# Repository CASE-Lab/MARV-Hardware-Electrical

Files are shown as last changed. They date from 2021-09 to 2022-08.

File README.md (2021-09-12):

# MARV-Hardware-Electrical
Contains the electrical design files fo the MARV system. These includes the PCBs and system wiring diagram and specific wire function diagram. Some of the PCB projects includes a component library, otherwise the CASE-Association case-eagle-libraries have been used, found here: https://github.com/CASE-Association/case-eagle-libraries.git

This project uses both Eagle and KiCad ECAD programs. This is shown by folder names.

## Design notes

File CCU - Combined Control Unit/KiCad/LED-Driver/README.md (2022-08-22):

# MIDI Fuse LED Driver

Led driver with integrated eFuse and PWM dimming in a MIDI fuse format. Provides undervoltage cutoff for battery protection and a low standby current of 30 uA.

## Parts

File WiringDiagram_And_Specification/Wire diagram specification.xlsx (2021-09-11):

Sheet: Wire diagram specification
Reference | Name | Number of wires | Function | Connector 1 | Pin on Connector 1 | Wire color | Wire Marking | Connector 2 | Pin on Connector 2 | Flag | Length | AWG/mm^2 | DR Shrink | Est Length (m) | Total Est Length (m) | Bundle Diameter (mm) | Bundle Diameter | Deutsch Contact Type1 | Deutsch Contact Type2
Drive-By-Wire system
W1 | APS ECM (OUT) | 9 | APS 1 - VCC 5V | DTM04-12PA | 1 | White | VCC1 | DRC26-50S01 | 34 | W1, APS ECM | 0.9 m | 18 AWG | Type 3/8 (0.375) | 0.7 | 6.3 | 5.4 | 0.212598425 | 0462-005-20141 (DTM/DRC,F) | 0462-005-20141 (DTM/DRC,F)
 |  |  | APS 1 - GND |  | 2 | White | GND1 |  | 24
 |  |  | APS 1 - Signal |  | 3 | White | SIG1 |  | 14
 |  |  | APS 2 - VCC 5V |  | 4 | White | VCC2 |  | 23
 |  |  | APS 2 - GND |  | 6 | White | GND2 |  | 13
 |  |  | APS 2 - Signal |  | 5 | White | SIG2 |  | 4
 |  |  | APS Fully closed/open - VCC 5V |  | 7 | White | VCC3 |  | 12
 |  |  | APS Fully closed/open - GND |  | 8 | White | GND3 |  | 2
 |  |  | APS Fully closed/open - Signal |  | 9 | White | SIG3 |  | 3
W2 | APS Handle (IN) | 9 | APS 1 - VCC 5V | DTM06-12SA | 1 | White | VCC1 | DRC26-50S01 | 43 | W2, APS HAND | 0.9 m | 18 AWG | Type 3/8 (0.375) | 0.7 | 6.3 |  |  | 0460-010-20141 (DTM/DRC,M) | 0462-005-20141 (DTM/DRC,F)
 |  |  | APS 1 - GND |  | 2 | White | GND1 |  | 33
 |  |  | APS 1 - Signal |  | 3 | White | SIG1 |  | 42
 |  |  | APS 2 - VCC 5V |  | 4 | White | VCC2 |  | 32
 |  |  | APS 2 - GND |  | 6 | White | GND2 |  | 22
 |  |  | APS 2 - Signal |  | 5 | White | SIG2 |  | 41
 |  |  | APS Fully closed/open - VCC 5V |  | 7 | White | VCC3 |  | 21
 |  |  | APS Fully closed/open - GND |  | 8 | White | GND3 |  | 11
 |  |  | APS Fully closed/open - Signal |  | 9 | White | SIG3 |  | 31
W3 | RPS ECM (OUT) | 6 | RPS 1 - VCC 5V | DTM04-08PA | 1 | White | VCC1 | DRC26-50S01 | 48 | W3, RPS ECM | 0.9 m | 18 AWG | Type 1/4 (0.25) | 0.7 | 4.2 | 4.409081537 | 0.1735858871 | 0462-005-20141 (DTM/DRC,F) | 0462-005-20141 (DTM/DRC,F)
 |  |  | RPS 1 - GND |  | 2 | White | GND1 |  | 49
 |  |  | RPS 1 - Signal |  | 3 | White | SIG1 |  | 50
 |  |  | RPS 2 - VCC 5V |  | 4 | White | VCC2 |  | 39
 |  |  | RPS 2 - GND |  | 5 | White | GND2 |  | 30
 |  |  | RPS 2 - Signal |  | 6 | White | SIG2 |  | 40
W4 | RPS Handle (IN) | 6 | RPS 1 - VCC 5V | DTM06-08SA | 1 | White | VCC1 | DRC26-50S01 | 47 | W4, RPS HAND | 0.9 m | 18 AWG | Type 1/4 (0.25) | 0.7 | 4.2 |  |  | 0460-010-20141 (DTM/DRC,M) | 0462-005-20141 (DTM/DRC,F)
 |  |  | RPS 1 - GND |  | 2 | White | GND1 |  | 38
 |  |  | RPS 1 - Signal |  | 3 | White | SIG1 |  | 37
 |  |  | RPS 2 - VCC 5V |  | 4 | White | VCC2 |  | 28
 |  |  | RPS 2 - GND |  | 5 | White | GND2 |  | 29
 |  |  | RPS 2 - Signal |  | 6 | White | SIG2 |  | 27
W5 | BUZZER ECM | 2 | VCC 12V | DTM04-3P | 1 | White | VCC | DRC26-50S01 | 16 | W5, BUZ ECM | 0.9 m | 18 AWG | Type 1/8 (0.125) | 0.7 | 1.4 | 2.545584412 | 0.1002198586 | 0462-005-20141 (DTM/DRC,F) | 0462-005-20141 (DTM/DRC,F)
 |  |  | GND |  | 2 | White | GND |  | 17
W6 | BUZZER Handle | 2 | VCC 12V | DTM06-3S | 1 | White | VCC | DRC26-50S01 | 6 | W6, BUZ HAND | 0.9 m | 18 AWG | Type 1/8 (0.125) | 0.7 | 1.4 |  |  | 0460-010-20141 (DTM/DRC,M) | 0462-005-20141 (DTM/DRC,F)
 |  |  | GND |  | 2 | White | GND |  | 7
W7 | Paddel Wheel ECM | 3 | VCC - 12V | DTM04-3P | 1 | White | VCC | DRC26-50S01 | 18 | W7, PW ECM | 0.9 m | 18 AWG | Type 3/16 (0.1875) | 0.7 | 2.1 | 3.117691454 | 0.1227437579 | 0462-005-20141 (DTM/DRC,F) | 0462-005-20141 (DTM/DRC,F)
 |  |  | GND |  | 2 | White | GND |  | 19
 |  |  | Signal |  | 3 | White | SIG |  | 20
W8 | Paddel Wheel Sensor | 3 | VCC - 12V | DTM06-3S | 1 | White | VCC | DRC26-50S01 | 8 | W8, PW SENS | 0.9 m | 18 AWG | Type 3/16 (0.1875) | 0.7 | 2.1 |  |  | 0460-010-20141 (DTM/DRC,M) | 0462-005-20141 (DTM/DRC,F)
 |  |  | GND |  | 2 | White | GND |  | 9
 |  |  | Signal |  | 3 | White | SIG |  | 10
W9 | Angle Sensor | 3 | GND | 282087-1 | 1 | White | GND | DT06-12SA | 3 | W9, ANG SENS | 0.95 m | 18 AWG | Type 3/16 (0.1875) | 1 | 3 |  |  |  | 0462-201-16141 (DT,F)
 |  |  | VCC -12V |  | 2 | White | VCC |  | 2
 |  |  | Signal |  | 3 | White | OUTPUT |  | 1
W10 | Motor | 4 | A1 | NA |  | Black | 2 | DT06-12SA | 10 | MOTOR |  |  |  | 1 | 4 |  |  |  | 0462-201-16141 (DT,F)
 |  |  | A2 |  |  | Black | 3 |  | 9
 |  |  | B1 |  |  | Black | 1 |  | 12
 |  |  | B2 |  |  | Black (Y/G) |  |  | 11
 |  |  | Cable Shield |  |  | White |  |  | 8
DB-W11 | DB Wire Harness | 6 | CAN_H | DT06-6S | 1 | Black, Yellow | CAN-H | DTM06-12SA | 1 | W11, DB | 1.2 m | 18 AWG | Type 3/8 (0.375) | 0.6 | 2.4 | 7.517978452 | 0.2959834033 | 0462-201-16141 (DT,F) | 0462-005-20141 (DTM/DRC,F)
 |  |  | CAN_L |  | 2 | Black, Green | CAN-L |  | 2 |  |  | CAN Cable |  | 0.6 | 0.6
 |  |  | 12V_AUTO |  | 3 | White | 12V-A |  | 3
 |  |  | GND |  | 4 | White | GND |  | 4
 |  |  | 12V |  | 5 | White | 12V |  | 5
 |  |  | GND |  | 6 | White | GND |  | 6
DB-W12 | DB Wire Harness | 6 | CAN_H | DTM06-12SA | 12 | Black, Yellow | CAN-H | DT06-06S-E008 | 1 | W12, DB | 2.2 m | 18 AWG | Type 3/8 (0.375) | 1.6 | 6.4 |  |  | 0462-005-20141 (DTM/DRC,F) | 0462-201-16141 (DT,F)
 |  |  | CAN_L |  | 11 | Black, Green | CAN-L |  | 2 |  |  | CAN Cable |  | 1.6 | 1.6
 |  |  | 12V_AUTO |  | 10 | White | 12V-A |  | 3
 |  |  | GND |  | 9 | White | GND |  | 4
 |  |  | 12V |  | 8 | White | 12V |  | 5
 |  |  | GND |  | 7 | White | GND |  | 6
W13 | OCU Mode Select | 4 | ? | DT06-4S | 1 | White | 1 | DT06-4S-E008 | 1 | W13, OCU MODE |  | 18 AWG | Type 1/4 (0.25) | 1 | 4 | 3.6 | 0.1417322833 | 0462-201-16141 (DT,F) | 0462-201-16141 (DT,F)
 |  |  | ? |  | 2 | White | 2 |  | 2
 |  |  | ? |  | 3 | White | 3 |  | 3
 |  |  | ? |  | 4 | White | 4 |  | 4
W14 | OCU Pedal | 2 | IN | DT06-2S-E008 | 1 | White | - | NA |  | W14, OCU PEDAL |  | 18 AWG | Type 1/8 (0.125) | 1.5 | 3 | 2.545584412 | 0.1002198586 |  | 0462-201-16141 (DT,F)
 |  |  | OUT |  | 2 | Green | -
W16 | ACU CAN | 2 | CAN_H | Y-Boot |  | Black, Yellow |  | PXMBNI12FIM04DSCPG7 | 4 | W16, ACU CAN |  | CAN Cable |  | 0.5 | 0.5 | 5.5 | 0.2165354329
 |  |  | CAN_L |  |  | Black, Green |  |  | 5
W17 | ACU Power | 4 | GND | Y-Boot |  | White | Black | T4111001041-000 | 1 | W17, ACU POW |  | 18 AWG | Type 1/4 (0.25) | 0.5 | 2 | 3.6 | 0.1417322833
 |  |  | GND |  |  | White | Black |  | 2
 |  |  | 12V |  |  | White | Red |  | 3
 |  |  | 12V |  |  | White | Red |  | 4
W18 | INS | 4 | ~~SYNC IN A – ODO B~~ | UP01L07 M010S BK1 Z2ZA | ~~1~~ | Black, Green |  | PXMBNI12FIM05ASCPG7 |  | W18, INS |  |  |  | 0.4 | 1.6 | -
 |  |  | ~~SYNC IN B – PORT B RX - ODO A ~~ |  | ~~2~~ | Black, Blue
 |  |  | VIN |  | 3 | Black, Red |  |  | 3
 |  |  | GND |  | 4 | Black, Black |  |  | 4
 |  |  | ~~PORT A RS-232/RS-422~~ |  | ~~5~~ | Black, N/A
 |  |  | ~~SYNC OUT A~~ |  | ~~6~~ | Black, Brown
 |  |  | ~~PORT E TX – PORT A RS422 TX+ ~~ |  | ~~7~~ | Black, White
 |  |  | PORT A RS232 TX – PORT A RS422 TX- |  | 8 | Black, Yellow |  |  | 1
 |  |  | PORT A RS232 RX – PORT A RS422 RX+ |  | 9 | Black, Orange |  |  | 2
 |  |  | ~~PORT E RX – PORT A RS422 RX- ~~ |  | ~~10~~ | Black, Grey
W19 | Fuse-Box-2 -> CCU | 4 | GND | DTP06-4S-E004 | 1 | Black |  | DTP06-4S-E004 | 3 | W19, PDU POW |  | 6mm2 |  | 0.5 | 2 | 8.88 | 0.3496062989 | 0462-203-12141 (DTP,F) | 0462-203-12141 (DTP,F)
 |  |  | GND |  | 2 | Black |  |  | 4
 |  |  | 12V |  | 3 | Red |  |  | 1
 |  |  | 12V |  | 4 | Red |  |  | 2
W20 | Aux battery -> Fuse-Box-2 | 2 | GND | NA | (-) | Black |  | PG7 2x | (-) | W20, AUX Bat-FB2 |  | 6mm2 |  | 0.2 | 0.4 | 6.279108217 | 0.2472089847
 |  |  | 12V |  | (+) | Red |  |  | (+)
W21 | Charger Con2 -> Aux battery | 2 | GND | DTP06-2S | 1 (-) | Black |  | NA | (-) | W21, CHA CON2-AUX Bat |  | 6mm2 |  | 3 | 6 |  |  | 0462-203-12141 (DTP,F)
 |  |  | 12V |  | 2 (+) | Red |  |  | (+)
W22 | Charger -> Charger Con2 | 2 | GND | NA | (-) | Black |  | DTP04-2P | 1 (-) | W22, CHA-CHA CON2 |  | 6mm2 |  | 0.2 | 0.4 |  |  |  | 0460-204-12141 (DTP,M)
 |  |  | 12V |  | (+) | Red |  |  | 2 (+)
W23 | Charger Con1 -> Charger | 2 | GND | DTP04-2P | 1 (-) | Black |  | NA | (-) | W23, CHA CON1-CHA |  | 6mm2 |  | 0.2 | 0.4 |  |  | 0460-204-12141 (DTP,M)
 |  |  | 12V |  | 2 (+) | Red |  |  | (+)
W24 | Fuse-Box-1 -> Charger Con1 | 2 | GND | DTP06-4S | 1 (-) | Black |  | DTP06-2S | 1 (-) | W24, FB1-CHA CON1 |  | 6mm2 |  | 0.4 | 0.8 |  |  | 0462-203-12141 (DTP,F) | 0462-203-12141 (DTP,F)
 |  |  | 12V |  | 3 (+) | Red |  |  | 2 (+)
W25 | Fuse-Box-1 -> Charge Battery Connector | 2 | GND | Ring Terminal M5 | B_OUT | White |  | DTP06-2S | 1 (-) | W25, CHARGER IN |  | 4mm2 |  | 1.5 | 3 |  |  | 0462-203-12141 (DTP,F) | 0462-203-12141 (DTP,F)
 |  |  | 12V | Ring Terminal M5 | A_OUT | White |  |  | 2 (+)
W26 | Start Battery -> Fuse-Box-1 | 2 | GND | NA | (-) | Black |  | PG7 2x | (-) | W26, STA BAT |  | 6mm2 |  | 0.5 | 1
 |  |  | 12V |  | (+) | Red |  |  | (+)
W27 | Fuse-Box-2 -> LED Button/Connectors | 4 | GND | NA | (-) | Black |  | DTM04-2PA 2x | 1 | W27, LED FB |  | 6mm2 |  | 0.5 | 2
 |  |  | GND |  | (-) | Black |  |  | 1
 |  |  | 12V |  | (+) | Red |  |  | 2
 |  |  | 12V |  | (+) | Red |  |  | 2
W28 | LED Back | 2 | GND | DTM04-2PA | 1 | Black |  | DTM06-2SA | 1 | W28, LED BCK |  | 6mm2 |  | 0.5 | 1
 |  |  | 12V |  | 2 | Red |  |  | 2
W29 | LED Front | 2 | GND | DTM04-2PA | 1 | Black |  | DTM06-2SA | 1 | W29, LED FRT |  | 6mm2 |  | 0.5 | 1
 |  |  | 12V |  | 2 | Red |  |  | 2
WaveRunner to Drive-By-Wire system
W27,W28 | APS | 9 | APS 1 - VCC 5V | DTM04-12PA, DTM06-12SA | 1 | (O/R) - Orange/Red |  |  |  | W27, APS ECM / W28, APS HAND
 |  |  | APS 1 - GND |  | 2 | (B/R) - Black/Red
 |  |  | APS 1 - Signal |  | 3 | (P/R) - Pink/Red
 |  |  | APS 2 - VCC 5V |  | 4 | (O/W) - Orange/White
 |  |  | APS 2 - Signal |  | 6 | (P/W) - Pink/White
 |  |  | APS 2 - GND |  | 5 | (B/W) - Black/White
 |  |  | APS Fully closed/open - VCC 5V |  | 7 | (O/G) - Orange/Green
 |  |  | APS Fully closed/open - GND |  | 8 | (B/G) - Black/Green
 |  |  | APS Fully closed/open - Signal |  | 9 | (P/G) - Pink/Green
W29/W30 | RPS | 6 | RPS 1 - VCC 5V | DTM04-08PA, DTM06-08SA | 1 | (O/R) - Orange/Red |  |  |  | W29, RPS ECM / W30, RPS HAND
 |  |  | RPS 1 - GND |  | 2 | (B/R) - Black/Red
 |  |  | RPS 1 - Signal |  | 3 | (P/R) - Pink/Red
 |  |  | RPS 2 - VCC 5V |  | 4 | (O/W) - Orange/White
 |  |  | RPS 2 - GND |  | 5 | (B/W) - Black/White
 |  |  | RPS 2 - Signal |  | 6 | (P/W) - Pink/White
W31/W32 | Buzzer | 2 | VCC - 12V | DTM04-3P, DTM06-3S | 1 | (R) - Red |  |  |  | W31, BUZ ECM / W32, BUZ HAND
 |  |  | GND |  | 2 | (B) - Black
W33/W34 | Paddel Wheel | 3 | VCC - 12V | DTM04-3P, DTM06-3S | 1 | (R/W) - Red/White (or Red/Yellow) |  |  |  | W33, PW ECM / W34, PW SENS
 |  |  | GND |  | 2 | (B/Y) - Black/Yellow
 |  |  | Signal |  | 3 | (Y) - Yellow
WaveRunner - Decawave Positioning System
W35 | ACU USB -> Decawave Hub Unit (DHU) | 5 | VCC - 5V | ACU USB1 - (Cable PX0441/2M00) | 1 | Red |  | PX0446 | 1 | W35, DHU
 |  |  | D- |  | 2 | White |  |  | 2
 |  |  | D+ |  | 3 | Green |  |  | 3
 |  |  | GND |  | 4 | Black |  |  | 4
 |  |  | Shield |  | 5 | Black |  |  | 5
W36/W37/W38 | DHU -> Decawave Sensor Unit (DSU), Anchors | 8 | GND | Cable Gland - (Cable 1404181) | 1 | White |  | PXMBNI08FPF08AFLM11002 | 1 | W36, DSU_A1 / W37, DSU_A2, W38, DSU_A3
 |  |  | VCC - 5V |  | 2 | Brown |  |  | 2
 |  |  | RS_232_TX (DHU) |  | 3 | Green |  |  | 3
 |  |  | RS_232_RX (DHU) |  | 4 | Yellow |  |  | 4
 |  |  | SWDIO |  |  | Grey |  |  | 5
 |  |  | SWCLK |  |  | Pink |  |  | 6
 |  |  | NRST |  |  | Blue |  |  | 7
W39 | ACU ES -> Decawave Sensor Unit, Passive tag | 8 | GND | PXMBNI12FIM05BSCPG7 | 4 | White |  | PXMBNI08FPF08AFLM11002 | 1 | W39, DSU_PT
 |  |  | VCC - 5V |  | 3 | Brown |  |  | 2
 |  |  | RS_232_TX (ACU ES) |  | 2 | Green |  |  | 3
 |  |  | RS_232_RX (ACU ES) |  | 1 | Yellow |  |  | 4
 |  |  | SWDIO |  |  | Grey |  |  | 5
 |  |  | SWCLK |  |  | Pink |  |  | 6
 |  |  | NRST |  |  | Blue |  |  | 7
 |  |  |  |  |  | Red |  |  | 8
W40/W41 | DHU Harbour -> DSU Harbour tags | 8 | GND | Cable Gland - (Cable 1404181) | 1 | White |  | PXMBNI08FPF08AFLM11002 | 1 | W40, DSU_T1 / W41, DSU_T2
 |  |  | VCC - 5V |  | 2 | Brown |  |  | 2
 |  |  | RS_232_TX (DHU) |  | 3 | Green |  |  | 3
 |  |  | RS_232_RX (DHU) |  | 4 | Yellow |  |  | 4
 |  |  | SWDIO |  |  | Grey |  |  | 5
 |  |  | SWCLK |  |  | Pink |  |  | 6
 |  |  | NRST |  |  | Blue |  |  | 7
 |  |  |  |  |  | Red |  |  | 8

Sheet: Pins, Tube, Wire length
Cable Types | Cable Diameter (mm) | Total Cable Length | DR25 Types | Total DR25 Length | Contact Types | Deutsch Nbr of Contacts | Deutsch Sealing Plugs
CAN Cable | 5.5 | 2.7 | Type 1/8 (0.125) | 2.9 | 0462-005-20141 (DTM/DRC,F) | 72 | 0413-204-2005 (DTM/DRC) = 35
18 AWG | 1.5 | 48.8 | Type 3/16 (0.1875) | 2.4 | 0460-010-20141 (DTM/DRC,M) | 20 | 0413-003-1605 (DT) = 25
6mm2 | 3.7 | 15 | Type 1/4 (0.25) | 2.9 | 0462-201-16141 (DT,F) | 29 | 114017-ZZ (DTP) = 6
 |  |  | Type 3/8 (0.375) | 3.6 | 0460-202-16141 (DT,M) | 0
 |  |  | Type 1/2 (0.5) | 0 | 0462-203-12141 (DTP,F) | 18
 |  |  |  |  | 0460-204-12141 (DTP,M) | 4

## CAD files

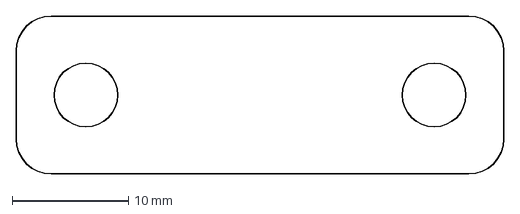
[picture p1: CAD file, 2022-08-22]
CCU - Combined Control Unit/KiCad/LED-Driver/fuseMIDIOutline.dxf
42.0 x 13.6 mm

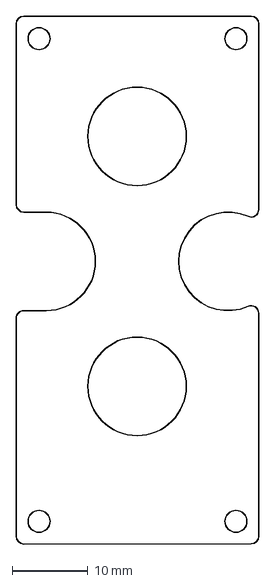
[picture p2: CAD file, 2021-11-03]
OCU - Operator Control Unit/Eagle/OCU_Buttons_Adapter_Rev1/BUTTONS_ADAPTER_PCB_OULINE.dxf
32.0 x 69.7 mm

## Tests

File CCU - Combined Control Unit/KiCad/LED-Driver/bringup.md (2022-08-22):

# Bringup notes LED Driver

## REV 1

* 68 nF for 180 Hz PWM frequency (with 100 k potentiometer)
* Approx 30 uA off current when switch open (off)
* Approx 400 uA (higher than expected?) when switch closed and battery in undervoltage (set to 10 V).
* Solid on/off operation at 13.2 volt and above. There is a band where PWM operation seems unreliable but still not clear why (Dampening decoupling needed?)?

- [ ] Check what the calculated on/off voltages should be
- [ ] Try with long LED strip to verify stability

If the PWM circuit gives to much trouble just convert to on/off control only by removing and installing jumper instead of mosfet.

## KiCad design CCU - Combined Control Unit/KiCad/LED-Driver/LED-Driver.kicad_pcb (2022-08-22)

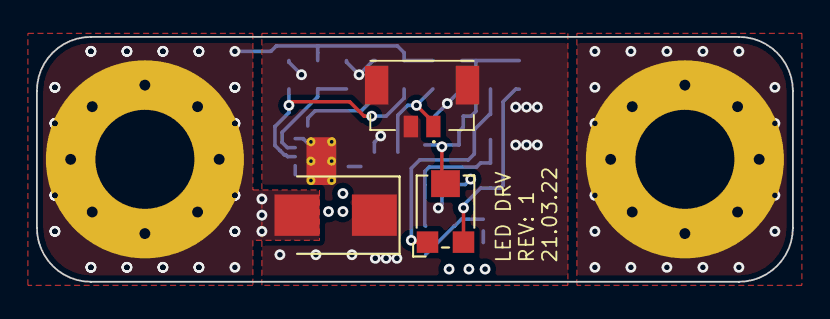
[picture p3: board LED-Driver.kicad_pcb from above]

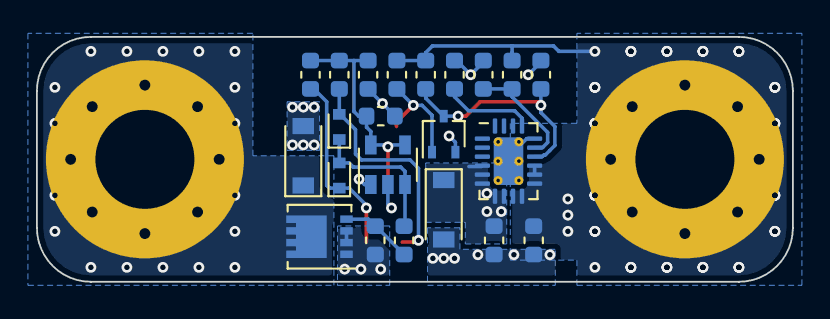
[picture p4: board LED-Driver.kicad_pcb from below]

Board: 4 copper layers, 42.0 x 13.6 mm, 27 parts (22 on the bottom side), 13 nets.

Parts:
C1, C2: 0.1 uF; C_0603_1608Metric
C3: 2.2uF 16V; C_0603_1608Metric
C4: ?; C_0603_1608Metric
D1, D5: D_Schottky; D_SOD-123
D2, D3: RB751S40T5G; D_SOD-523
D4: D_TVS; D_SMB
J1, J2: Conn_01x01; MountingHole_5.5mm_Pad_Via
J3: Conn_01x02; Molex_Micro-Lock_5055680271_1x02_P1.25_Vertical
Q1: 2N7002PW; SOT-323_SC-70
Q2: DMP3013SFV; Diodes_PowerDI3333-8
R1: 130k; R_0603_1608Metric
R2, R5: 1.5M; R_0603_1608Metric
R3, R6, R9: 100k; R_0603_1608Metric
R4: 18k; R_0603_1608Metric
R7, R8: R; R_0603_1608Metric
R10: 1k; R_0603_1608Metric
RV1: 100k; Potentiometer_Bourns_TC33X_Vertical
U1: MIC1555YM5-TR; SOT-23-5
U2: TPS25940x-Q1; QFN-20-1EP_3x4mm_P0.5mm_EP1.65x2.65mm_ThermalVias

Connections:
+12V: C1.1, D1.1, Q2.1, Q2.2, Q2.3, R9.2, U1.1, U2.4, U2.5, U2.6, U2.7, U2.8
+BATT: C2.1, D4.2, J1.1, R2.1, R5.1, R6.1, U2.9, U2.10, U2.11, U2.12, U2.13
/GATE: Q2.4, R9.1, R10.1
/LED_OUT: D5.1, J2.1, Q2.5
/PWM: D2.2, D3.1, R10.2, U1.3
/TRG_THR: C3.1, C4.1, R7.2, R8.2, RV1.2, U1.4, U1.5
/eFuse/~EN: J3.1, Q1.1, R6.2
GND: C1.2, C2.2, C3.2, C4.2, D1.2, D4.1, D5.2, J3.2, J3.MP, Q1.2, R1.2, R3.2, R4.2, U1.2, U2.16, U2.21
unnamed: D2.1, R7.1, RV1.3
unnamed: D3.2, R8.1, RV1.1
unnamed: Q1.3, R1.1, R5.2, U2.14
unnamed: R2.2, R3.1, U2.15
unnamed: R4.1, U2.17

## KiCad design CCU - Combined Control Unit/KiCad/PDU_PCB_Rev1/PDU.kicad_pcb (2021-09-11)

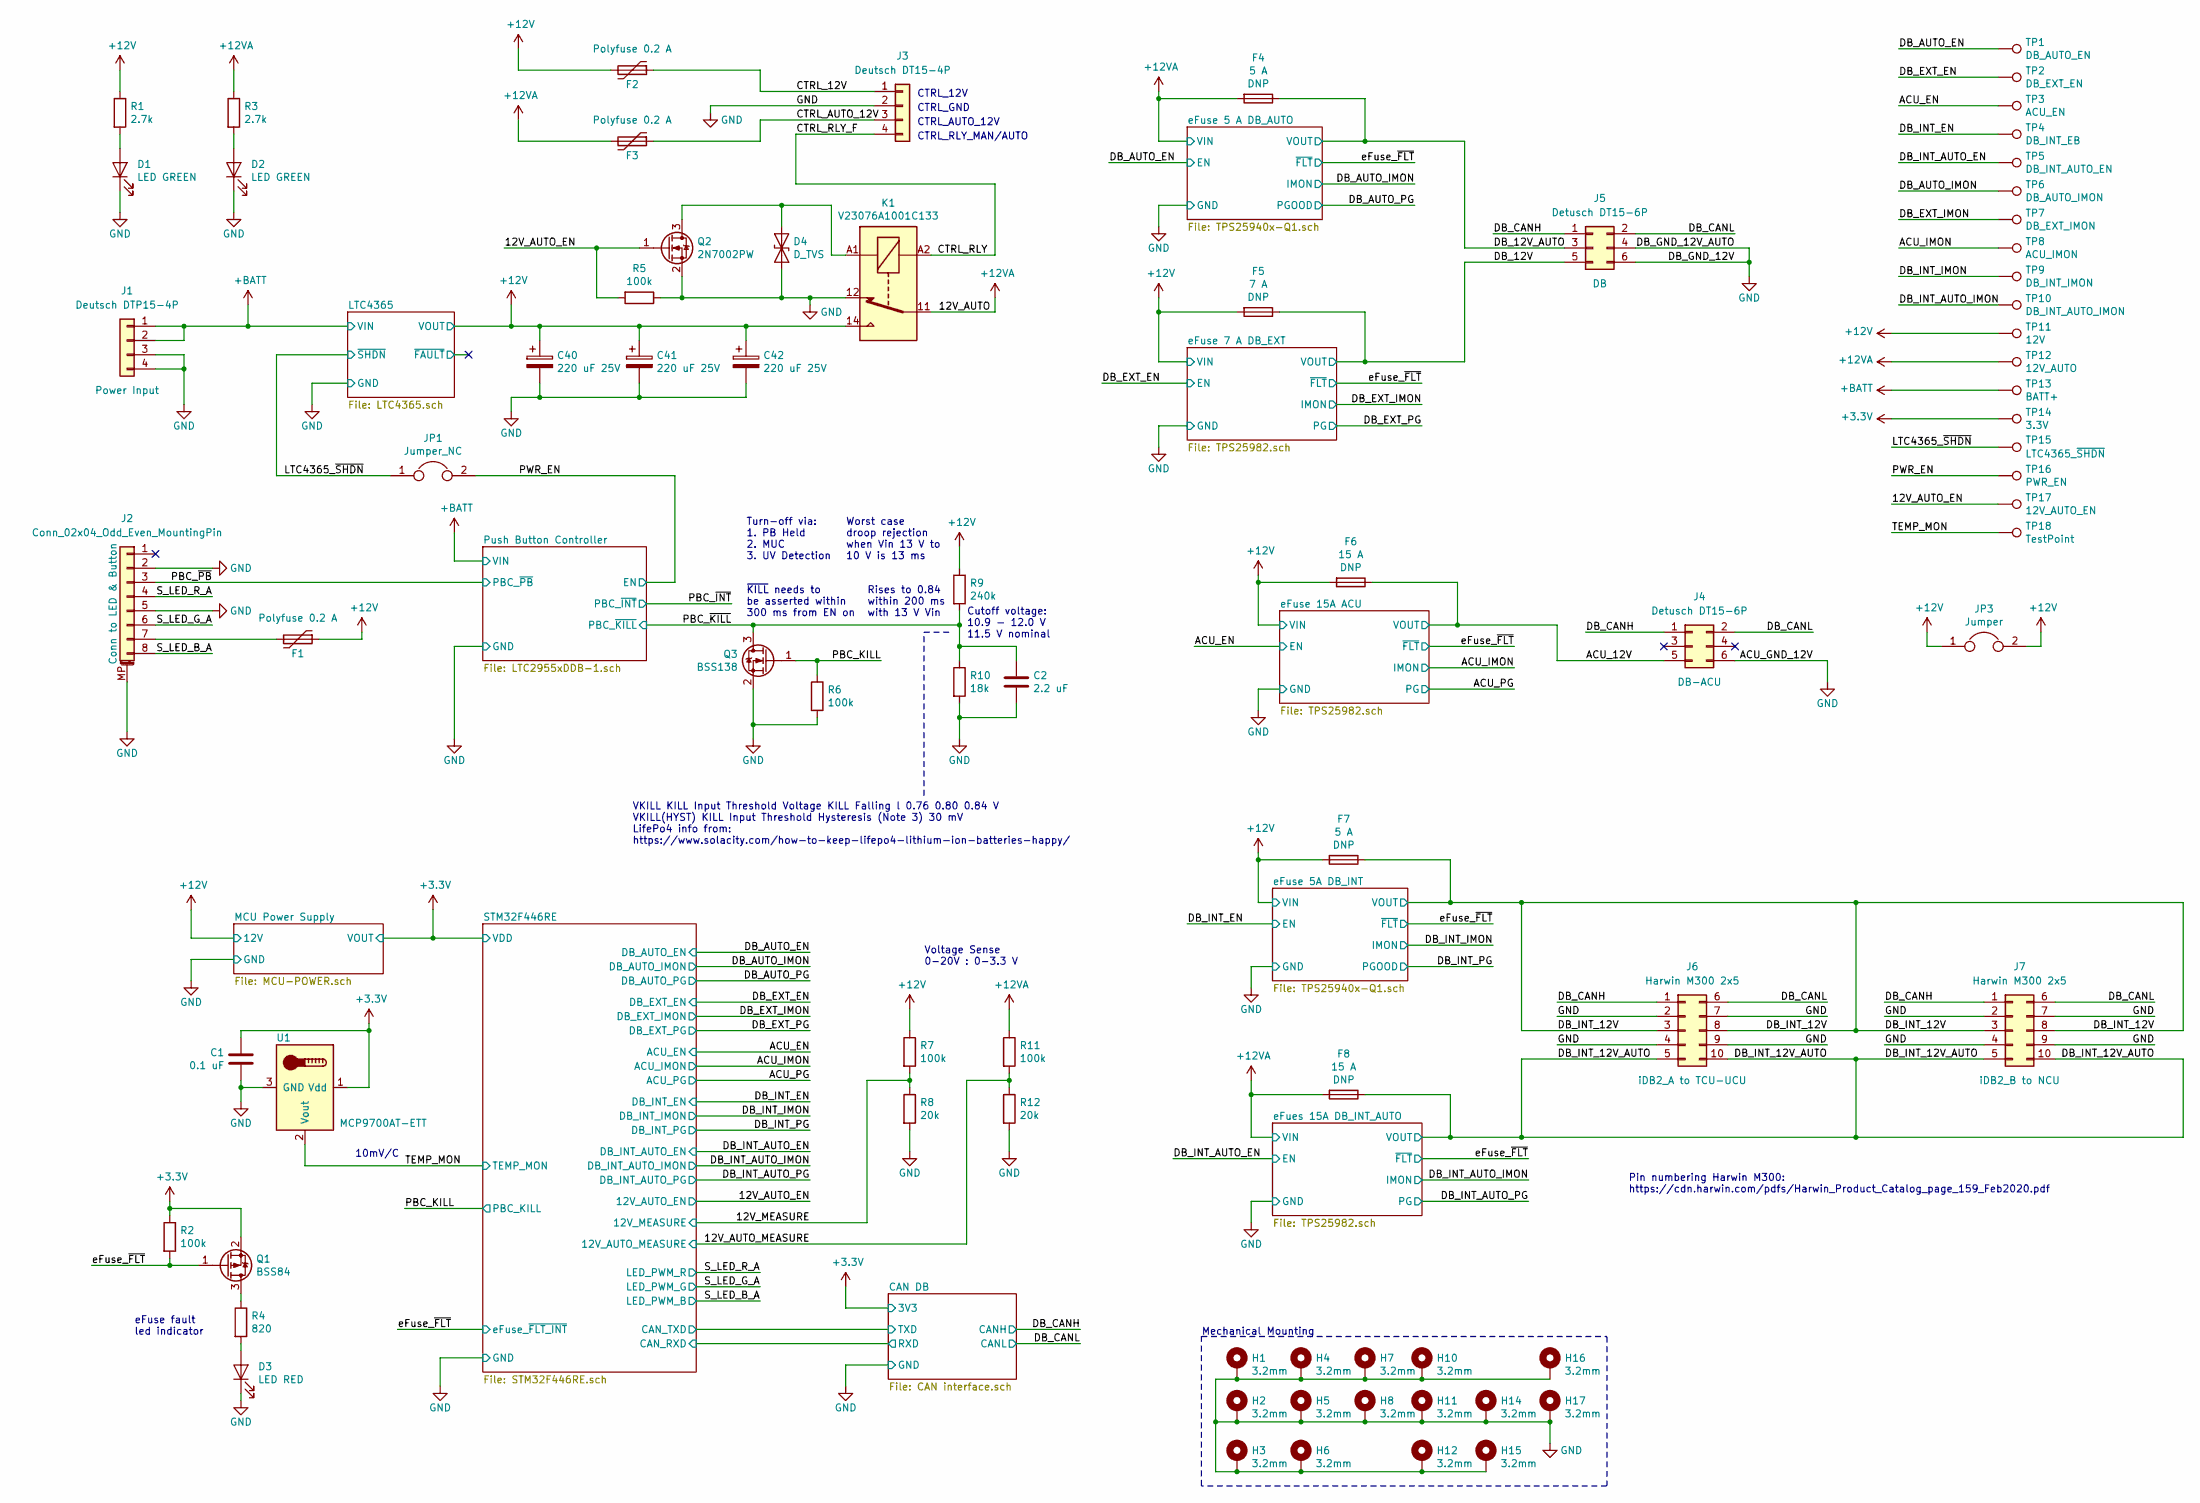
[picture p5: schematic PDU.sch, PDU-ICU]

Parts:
C1: 0.1 uF; C_0603_1608Metric
C2: 2.2 uF; C_0603_1608Metric
C40, C41, C42: 220 uF 25V; CP_Radial_D8.0mm_P3.50mm; MPN ESE227M025AG3AA
D1, D2: LED GREEN; LED_0603_1608Metric
D3: LED RED; LED_0603_1608Metric
D4: D_TVS; D_SMB; MPN TPSMB20CA
F1, F2, F3: Polyfuse 0.2 A; R_1206_3216Metric; MPN NANOSMDC020F-2
F4, F7: 5 A; Fuse_2010_5025Metric_Pad1.52x2.65mm_HandSolder; MPN 0453005
F5: 7 A; Fuse_2010_5025Metric_Pad1.52x2.65mm_HandSolder; MPN 0453007
F6, F8: 15 A; Fuse_2010_5025Metric_Pad1.52x2.65mm_HandSolder; MPN 0453012
H1, H2, H3, H4, H5, H6, H7, H8, H10, H11, H12, H14, H15, H16, H17: 3.2mm; MountingHole_3.2mm_M3_Pad_Via
J1: Deutsch DTP15-4P; Deutsch_DTP15-4P_2x2
J2: Conn_02x04_Odd_Even_MountingPin; Molex_Micro-Lock_5054330871_2x4_P1.25_Vertical; MPN 538-505433-0871
J3: Deutsch DT15-4P; Deutsch_DT15-4P_2x2
J4, J5: Detusch DT15-6P; Detusch_DT15-6P_2x3
J6, J7: Harwin M300 2x5; Harwin_M300_M300MV31045M1_2x5_P3.0_Vertical
JP1: Jumper_NC; R_0603_1608Metric
JP3: Jumper; Keystone_5104; MPN 5104
K1: V23076A1001C133; TE_Relay_V23076A1001C133
Q1: BSS84; SOT-23; MPN BSS84
Q2: 2N7002PW; SOT-323_SC-70
Q3: BSS138; SOT-23
R1, R3: 2.7k; R_0603_1608Metric
R2, R5, R6, R7, R11: 100k; R_0603_1608Metric
R4: 820; R_0603_1608Metric
R8, R12: 20k; R_0603_1608Metric
R9: 240k; R_0603_1608Metric
R10: 18k; R_0603_1608Metric
TP1: DB_AUTO_EN; TestPoint_THTPad_D1.0mm_Drill0.5mm
TP2: DB_EXT_EN; TestPoint_THTPad_D1.0mm_Drill0.5mm
TP3: ACU_EN; TestPoint_THTPad_D1.0mm_Drill0.5mm
TP4: DB_INT_EB; TestPoint_THTPad_D1.0mm_Drill0.5mm
TP5: DB_INT_AUTO_EN; TestPoint_THTPad_D1.0mm_Drill0.5mm
TP6: DB_AUTO_IMON; TestPoint_THTPad_D1.0mm_Drill0.5mm
TP7: DB_EXT_IMON; TestPoint_THTPad_D1.0mm_Drill0.5mm
TP8: ACU_IMON; TestPoint_THTPad_D1.0mm_Drill0.5mm
TP9: DB_INT_IMON; TestPoint_THTPad_D1.0mm_Drill0.5mm
TP10: DB_INT_AUTO_IMON; TestPoint_THTPad_D1.0mm_Drill0.5mm
TP11: 12V; TestPoint_THTPad_D1.0mm_Drill0.5mm
TP12: 12V_AUTO; TestPoint_THTPad_D1.0mm_Drill0.5mm
TP13: BATT+; TestPoint_THTPad_D1.0mm_Drill0.5mm
TP14: 3.3V; TestPoint_THTPad_D1.0mm_Drill0.5mm
TP15: LTC4365_~SHDN; TestPoint_THTPad_D1.0mm_Drill0.5mm
TP16: PWR_EN; TestPoint_THTPad_D1.0mm_Drill0.5mm
TP17: 12V_AUTO_EN; TestPoint_THTPad_D1.0mm_Drill0.5mm
TP18: TestPoint; TestPoint_THTPad_D1.0mm_Drill0.5mm
U1: MCP9700AT-ETT; SOT-23; MPN MCP9700AT-E/TT

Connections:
+3V3: C1.1, Q1.2 (S), R2.1, TP14.1, U1.1 (Vdd); also elsewhere on the board
+12V: C40.1, C41.1, C42.1, F1.1, F2.2, F5.2, F6.2, F7.2, JP3.1, JP3.2, K1.14, R1.1, R7.1, R9.1, TP11.1; also elsewhere on the board
+12VA: F3.2, F4.2, F8.2, K1.11, R3.1, R11.1, TP12.1; also elsewhere on the board
+BATT: J1.1, J1.2, TP13.1; also elsewhere on the board
/12V_AUTO_EN: Q2.1 (G), R5.2, TP17.1; also elsewhere on the board
/12V_AUTO_MEASURE: R11.2, R12.1; also elsewhere on the board
/12V_MEASURE: R7.2, R8.1; also elsewhere on the board
/ACU_12V: F6.1, J4.5; also elsewhere on the board
/ACU_EN: TP3.1; also elsewhere on the board
/ACU_IMON: TP8.1; also elsewhere on the board
/CTRL_12V: F2.1, J3.1
/CTRL_AUTO_12V: F3.1, J3.3
/CTRL_RLY: J3.4, K1.A2
/DB_AUTO_EN: TP1.1; also elsewhere on the board
/DB_AUTO_IMON: TP6.1; also elsewhere on the board
/DB_CANH: J4.1, J5.1, J6.1, J7.1; also elsewhere on the board
/DB_CANL: J4.2, J5.2, J6.6, J7.6; also elsewhere on the board
/DB_EXT_EN: TP2.1; also elsewhere on the board
/DB_EXT_IMON: TP7.1; also elsewhere on the board
/DB_INT_AUTO_EN: TP5.1; also elsewhere on the board
/DB_INT_AUTO_IMON: TP10.1; also elsewhere on the board
/DB_INT_EN: TP4.1; also elsewhere on the board
/DB_INT_IMON: TP9.1; also elsewhere on the board
/LTC4365_~SHDN: JP1.1, TP15.1; also elsewhere on the board
/PBC_KILL: Q3.1 (G), R6.1; also elsewhere on the board
/PBC_~KILL: C2.1, Q3.3 (D), R9.2, R10.1; also elsewhere on the board
/PBC_~PB: J2.3; also elsewhere on the board
/PWR_EN: JP1.2, TP16.1; also elsewhere on the board
/S_LED_B_A: J2.8; also elsewhere on the board
/S_LED_G_A: J2.6; also elsewhere on the board
/S_LED_R_A: J2.4; also elsewhere on the board
/TEMP_MON: TP18.1, U1.2 (Vout); also elsewhere on the board
/eFuse_~FLT: Q1.1 (G), R2.2; also elsewhere on the board
GND: C1.2, C2.2, C40.2, C41.2, C42.2, D1.1 (K), D2.1 (K), D3.1 (K), D4.2 (A2), H1.1, H2.1, H3.1, H4.1, H5.1, H6.1, H7.1, H8.1, H10.1, H11.1, H12.1, H14.1, H15.1, H16.1, H17.1, J1.3, J1.4, J2.2, J2.5, J2.MP (MountPin), J3.2, J4.6, J5.4, J5.6, J6.2, J6.4, J6.7, J6.9, J7.2, J7.4, J7.7, J7.9, K1.12, Q2.2 (S), Q3.2 (S), R5.1, R6.2, R8.2, R10.2, R12.2, U1.3 (GND); also elsewhere on the board
unnamed: D1.2 (A), R1.2
unnamed: D2.2 (A), R3.2
unnamed: D3.2 (A), R4.2
unnamed: D4.1 (A1), K1.A1, Q2.3 (D)
unnamed: F1.2, J2.7
unnamed: Q1.3 (D), R4.1

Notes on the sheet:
Mechanical Mounting
CTRL_12V
CTRL_GND
CTRL_AUTO_12V
CTRL_RLY_MAN/AUTO
Turn-off via: 1. PB Held 2. MUC 3. UV Detection
Pin numbering Harwin M300: https://cdn.harwin.com/pdfs/Harwin_Product_Catalog_page_159_Feb2020.pdf
eFuse fault led indicator
Voltage Sense 0-20V : 0-3.3 V
10mV/C
VKILL KILL Input Threshold Voltage KILL Falling l 0.76 0.80 0.84 V VKILL(HYST) KILL Input Threshold Hysteresis (Note 3) 30 mV LifePo4 info from: https://www.solacity.com/how-to-keep-lifepo4-lithium-ion-batteries-happy/
Cutoff voltage: 10.9 - 12.0 V 11.5 V nominal
~KILL~ needs to be asserted within 300 ms from EN on
Rises to 0.84 within 200 ms with 13 V Vin
Worst case droop rejection when Vin 13 V to 10 V is 13 ms

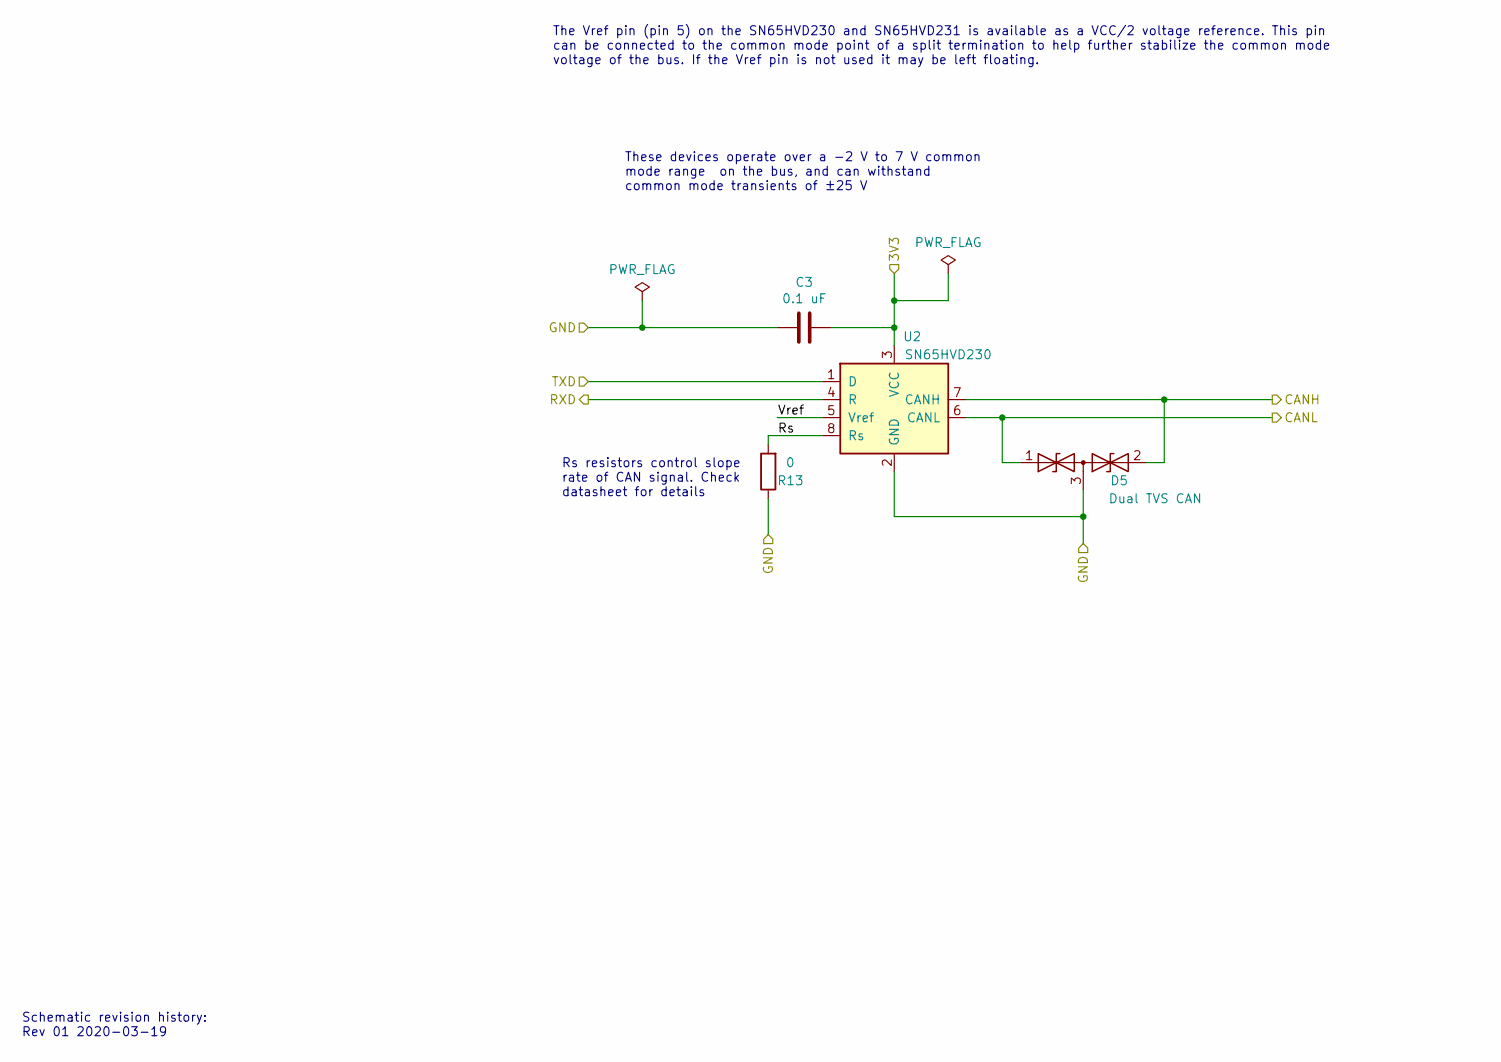
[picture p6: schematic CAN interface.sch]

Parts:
C3: 0.1 uF; C_0603_1608Metric
D5: Dual TVS CAN; SOT-23; MPN NUP2105L
R13: 0; R_0603_1608Metric
U2: SN65HVD230; SOIC-8_3.9x4.9mm_P1.27mm

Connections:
+3V3: C3.1, U2.3 (VCC); also elsewhere on the board
/CAN DB/Rs: R13.2, U2.8 (Rs)
/CAN DB/Vref: U2.5 (Vref)
/DB_CANH: D5.2 (A2), U2.7 (CANH); also elsewhere on the board
/DB_CANL: D5.1 (A1), U2.6 (CANL); also elsewhere on the board
/STM32F446RE/CAN_RXD: U2.4 (R); also elsewhere on the board
/STM32F446RE/CAN_TXD: U2.1 (D); also elsewhere on the board
GND: C3.2, D5.3 (common), R13.1, U2.2 (GND); also elsewhere on the board

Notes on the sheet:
These devices operate over a -2 V to 7 V common mode range on the bus, and can withstand common mode transients of ±25 V
Rs resistors control slope rate of CAN signal. Check datasheet for details
Schematic revision history: Rev 01 2020-03-19
The Vref pin (pin 5) on the SN65HVD230 and SN65HVD231 is available as a VCC/2 voltage reference. This pin can be connected to the common mode point of a split termination to help further stabilize the common mode voltage of the bus. If the Vref pin is not used it may be left floating.

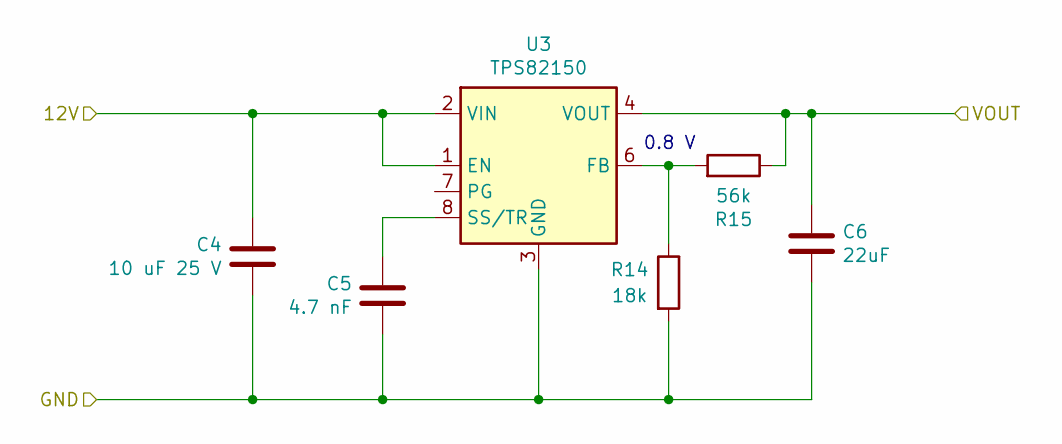
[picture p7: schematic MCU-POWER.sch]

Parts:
C4: 10 uF 25 V; C_1206_3216Metric
C5: 4.7 nF; C_0603_1608Metric
C6: 22uF; C_1206_3216Metric
R14: 18k; R_0603_1608Metric
R15: 56k; R_0603_1608Metric
U3: TPS82150; Texas_SIL0008D_MicroSiP-8-1EP_2.8x3mm_P0.65mm_EP1.1x1.9mm_T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; MPN TPS82150SILR

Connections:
+3V3: C6.1, R15.1, U3.4 (VOUT), U3.5 (VOUT); also elsewhere on the board
+12V: C4.1, U3.1 (EN), U3.2 (VIN); also elsewhere on the board
GND: C4.2, C5.2, C6.2, R14.2, U3.3 (GND), U3.9 (GND); also elsewhere on the board
unnamed: C5.1, U3.8 (SS/TR)
unnamed: R14.1, R15.2, U3.6 (FB)

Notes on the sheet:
0.8 V

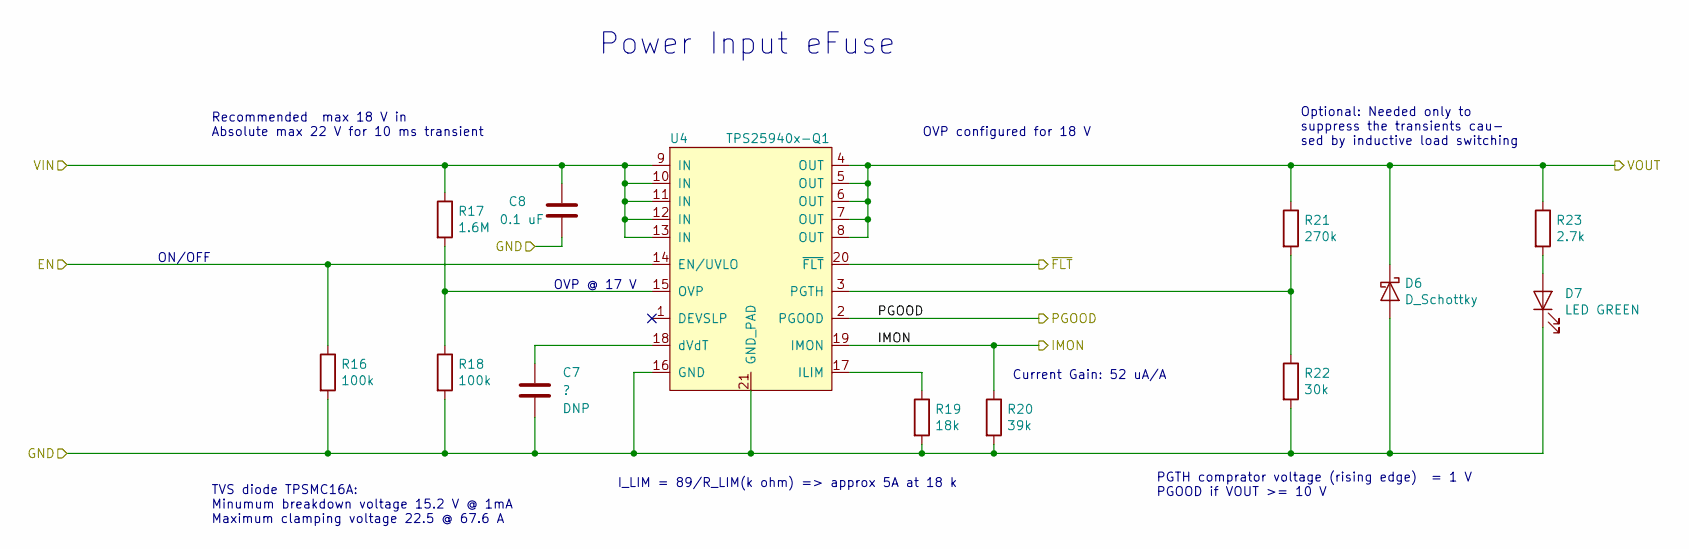
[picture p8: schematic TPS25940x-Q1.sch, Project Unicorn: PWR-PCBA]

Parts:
C7: ?; C_0603_1608Metric
C8: 0.1 uF; C_0603_1608Metric
D6: D_Schottky; D_SOD-123; MPN 1N5819HW
D17: LED GREEN; LED_0603_1608Metric
R16, R18: 100k; R_0603_1608Metric
R17: 1.6M; R_0603_1608Metric
R19: 18k; R_0603_1608Metric
R20: 39k; R_0603_1608Metric
R21: 270k; R_0603_1608Metric
R22: 30k; R_0603_1608Metric
R54: 2.7k; R_0603_1608Metric
U4: TPS25940x-Q1; QFN-20-1EP_3x4mm_P0.5mm_EP1.65x2.65mm_ThermalVias; MPN TPS25940LQRVCRQ1

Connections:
+12V: C8.1, R17.1, U4.9 (IN), U4.10 (IN), U4.11 (IN), U4.12 (IN), U4.13 (IN); also elsewhere on the board
/DB_INT_EN: R16.1, U4.14 (EN/UVLO); also elsewhere on the board
/DB_INT_IMON: R20.1, U4.19 (IMON); also elsewhere on the board
/DB_INT_PG: U4.2 (PGOOD); also elsewhere on the board
/eFuse_~FLT: U4.20 (~FLT); also elsewhere on the board
GND: C7.2, C8.2, D6.2 (A), D17.1 (K), R16.2, R18.2, R19.2, R20.2, R22.2, U4.16 (GND), U4.21 (GND_PAD); also elsewhere on the board
unnamed: C7.1, U4.18 (dVdT)
unnamed: D17.2 (A), R54.2
unnamed: R17.2, R18.1, U4.15 (OVP)
unnamed: R19.1, U4.17 (ILIM)
unnamed: R21.2, R22.1, U4.3 (PGTH)

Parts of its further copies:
C28: ?; C_0603_1608Metric
C29: 0.1 uF; C_0603_1608Metric
D7: LED GREEN; LED_0603_1608Metric
D16: D_Schottky; D_SOD-123; MPN 1N5819HW
R23: 2.7k; R_0603_1608Metric
R47, R49: 100k; R_0603_1608Metric
R48: 1.6M; R_0603_1608Metric
R50: 18k; R_0603_1608Metric
R51: 39k; R_0603_1608Metric
R52: 270k; R_0603_1608Metric
R53: 30k; R_0603_1608Metric
U10: TPS25940x-Q1; QFN-20-1EP_3x4mm_P0.5mm_EP1.65x2.65mm_ThermalVias; MPN TPS25940LQRVCRQ1

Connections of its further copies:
+12VA: C29.1, R48.1, U10.9 (IN), U10.10 (IN), U10.11 (IN), U10.12 (IN), U10.13 (IN); also elsewhere on the board
/DB_AUTO_EN: R47.1, U10.14 (EN/UVLO); also elsewhere on the board
/DB_AUTO_IMON: R51.1, U10.19 (IMON); also elsewhere on the board
/DB_AUTO_PG: U10.2 (PGOOD); also elsewhere on the board
/eFuse_~FLT: U10.20 (~FLT); also elsewhere on the board
GND: C28.2, C29.2, D7.1 (K), D16.2 (A), R47.2, R49.2, R50.2, R51.2, R53.2, U10.16 (GND), U10.21 (GND_PAD); also elsewhere on the board
unnamed: C28.1, U10.18 (dVdT)
unnamed: D7.2 (A), R23.2
unnamed: R48.2, R49.1, U10.15 (OVP)
unnamed: R50.1, U10.17 (ILIM)
unnamed: R52.2, R53.1, U10.3 (PGTH)

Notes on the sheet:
ON/OFF
Power Input eFuse
Recommended max 18 V in Absolute max 22 V for 10 ms transient
I_LIM = 89/R_LIM(k ohm) => approx 5A at 18 k
PGTH comprator voltage (rising edge) = 1 V PGOOD if VOUT >= 10 V
OVP configured for 18 V
Optional: Needed only to suppress the transients cau- sed by inductive load switching
TVS diode TPSMC16A: Minumum breakdown voltage 15.2 V @ 1mA Maximum clamping voltage 22.5 @ 67.6 A
OVP @ 17 V
Current Gain: 52 uA/A

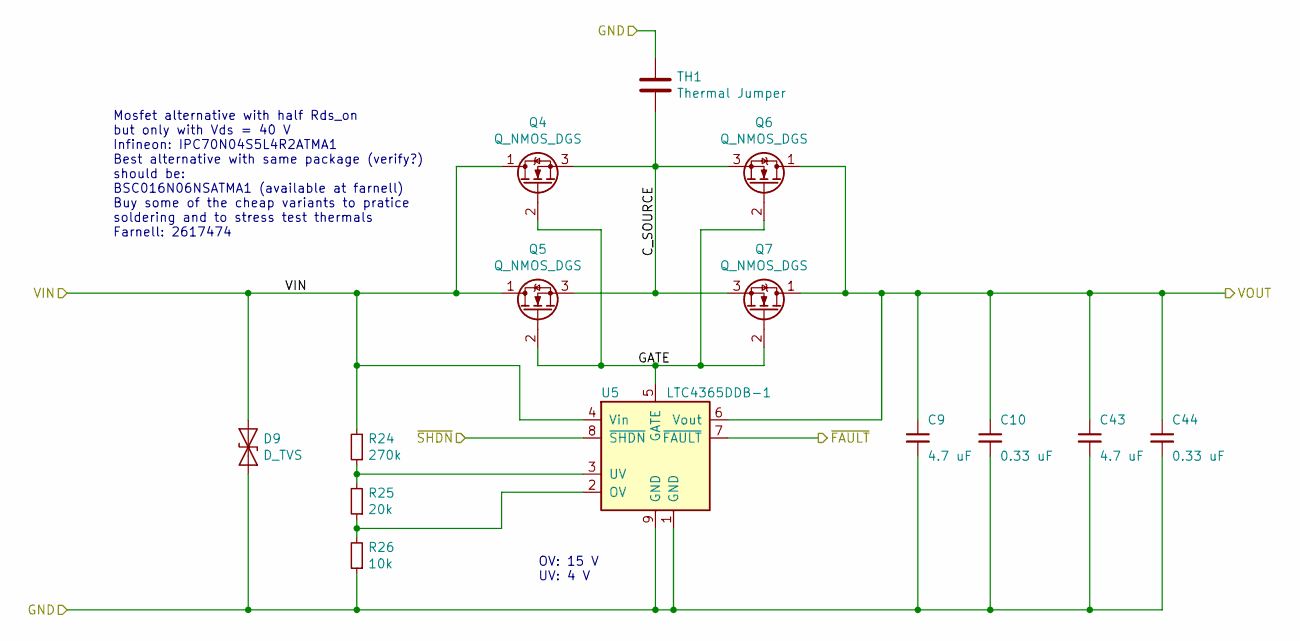
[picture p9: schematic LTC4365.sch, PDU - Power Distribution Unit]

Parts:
C9, C43: 4.7 uF; C_1206_3216Metric; MPN 12063C475K4T2A
C10, C44: 0.33 uF; C_0805_2012Metric
D9: D_TVS; D_SMC; MPN 5.0SMDJ24CA-Q
Q4, Q5, Q6, Q7: Q_NMOS_DGS; TDSON-8-1; MPN BSC016N06NSATMA1
R24: 270k; R_0603_1608Metric
R25: 20k; R_0603_1608Metric
R26: 10k; R_0603_1608Metric
TH1: Thermal Jumper; R_0612_1632Metric; MPN THJP0612AST1
U5: LTC4365DDB-1; DFN-8-1EP_2x3mm_P0.5mm_EP0.61x2.2mm; MPN LTC4365IDDB-1#TRMPBF

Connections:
+12V: C9.1, C10.1, C43.1, C44.1, Q6.1 (D), Q7.1 (D), U5.6 (Vout); also elsewhere on the board
+BATT: D9.1 (A1), Q4.1 (D), Q5.1 (D), R24.2, U5.4 (Vin); also elsewhere on the board
/LTC4365/C_SOURCE: Q4.3 (S), Q5.3 (S), Q6.3 (S), Q7.3 (S), TH1.2
/LTC4365/GATE: Q4.2 (G), Q5.2 (G), Q6.2 (G), Q7.2 (G), U5.5 (GATE)
/LTC4365/~FAULT: U5.7 (~FAULT)
/LTC4365_~SHDN: U5.8 (~SHDN); also elsewhere on the board
GND: C9.2, C10.2, C43.2, C44.2, D9.2 (A2), R26.1, TH1.1, U5.1 (GND), U5.9 (GND); also elsewhere on the board
unnamed: R24.1, R25.2, U5.3 (UV)
unnamed: R25.1, R26.2, U5.2 (OV)

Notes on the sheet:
OV: 15 V UV: 4 V
Mosfet alternative with half Rds_on but only with Vds = 40 V Infineon: IPC70N04S5L4R2ATMA1 Best alternative with same package (verify?) should be: BSC016N06NSATMA1 (available at farnell) Buy some of the cheap variants to pratice soldering and to stress test thermals Farnell: 2617474

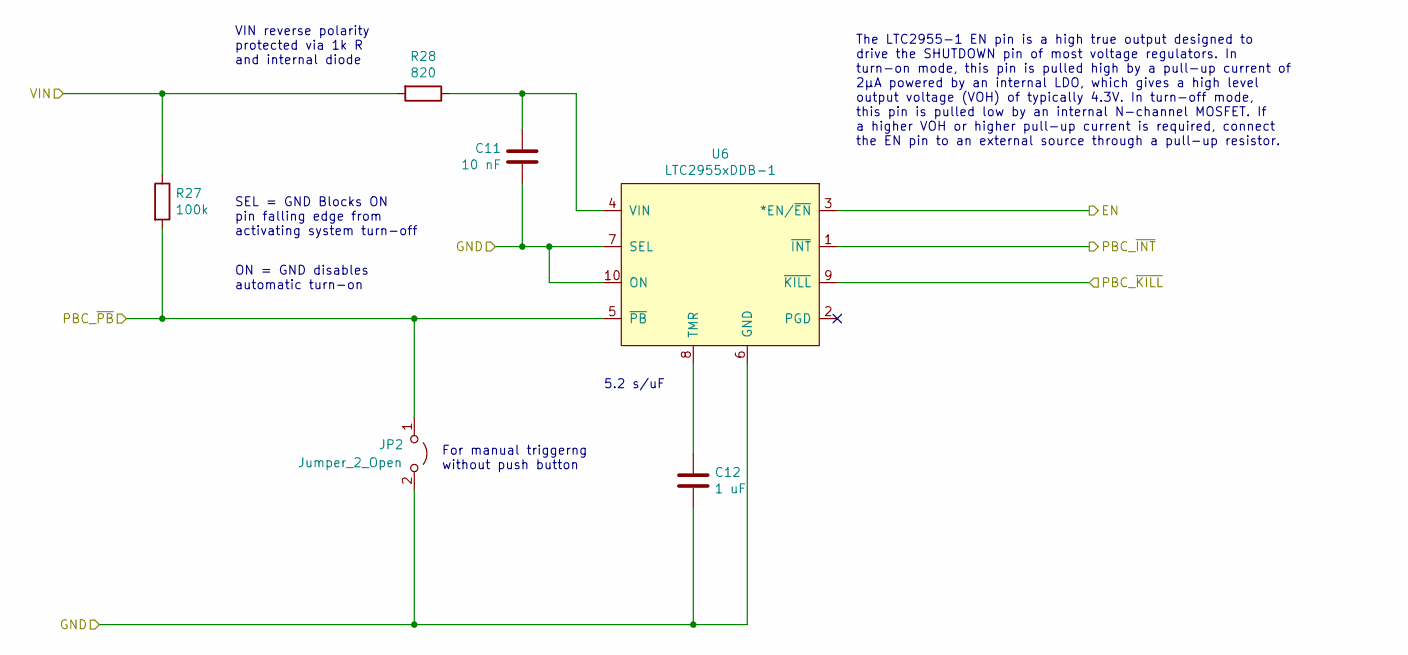
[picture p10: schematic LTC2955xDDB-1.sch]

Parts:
C11: 10 nF; C_0603_1608Metric
C12: 1 uF; C_0603_1608Metric
JP2: Jumper_2_Open; TestPoint_2Pads_Pitch2.54mm_Drill0.8mm
R27: 100k; R_0603_1608Metric
R28: 820; R_0603_1608Metric
U6: LTC2955xDDB-1; DFN-10-1EP_2x3mm_P0.5mm_EP0.64x2.4mm

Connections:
+BATT: R27.1, R28.2; also elsewhere on the board
/PBC_~INT: U6.1 (~INT)
/PBC_~KILL: U6.9 (~KILL); also elsewhere on the board
/PBC_~PB: JP2.1 (A), R27.2, U6.5 (~PB); also elsewhere on the board
/PWR_EN: U6.3 (*EN/~EN); also elsewhere on the board
GND: C11.2, C12.2, JP2.2 (B), U6.6 (GND), U6.7 (SEL), U6.10 (ON); also elsewhere on the board
unnamed: C11.1, R28.1, U6.4 (VIN)
unnamed: C12.1, U6.8 (TMR)

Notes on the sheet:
SEL = GND Blocks ON pin falling edge from activating system turn-off
5.2 s/uF
The LTC2955-1 EN pin is a high true output designed to drive the SHUTDOWN pin of most voltage regulators. In turn-on mode, this pin is pulled high by a pull-up current of 2µA powered by an internal LDO, which gives a high level output voltage (VOH) of typically 4.3V. In turn-off mode, this pin is p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
VIN reverse polarity protected via 1k R and internal diode
ON = GND disables automatic turn-on
For manual triggerng without push button

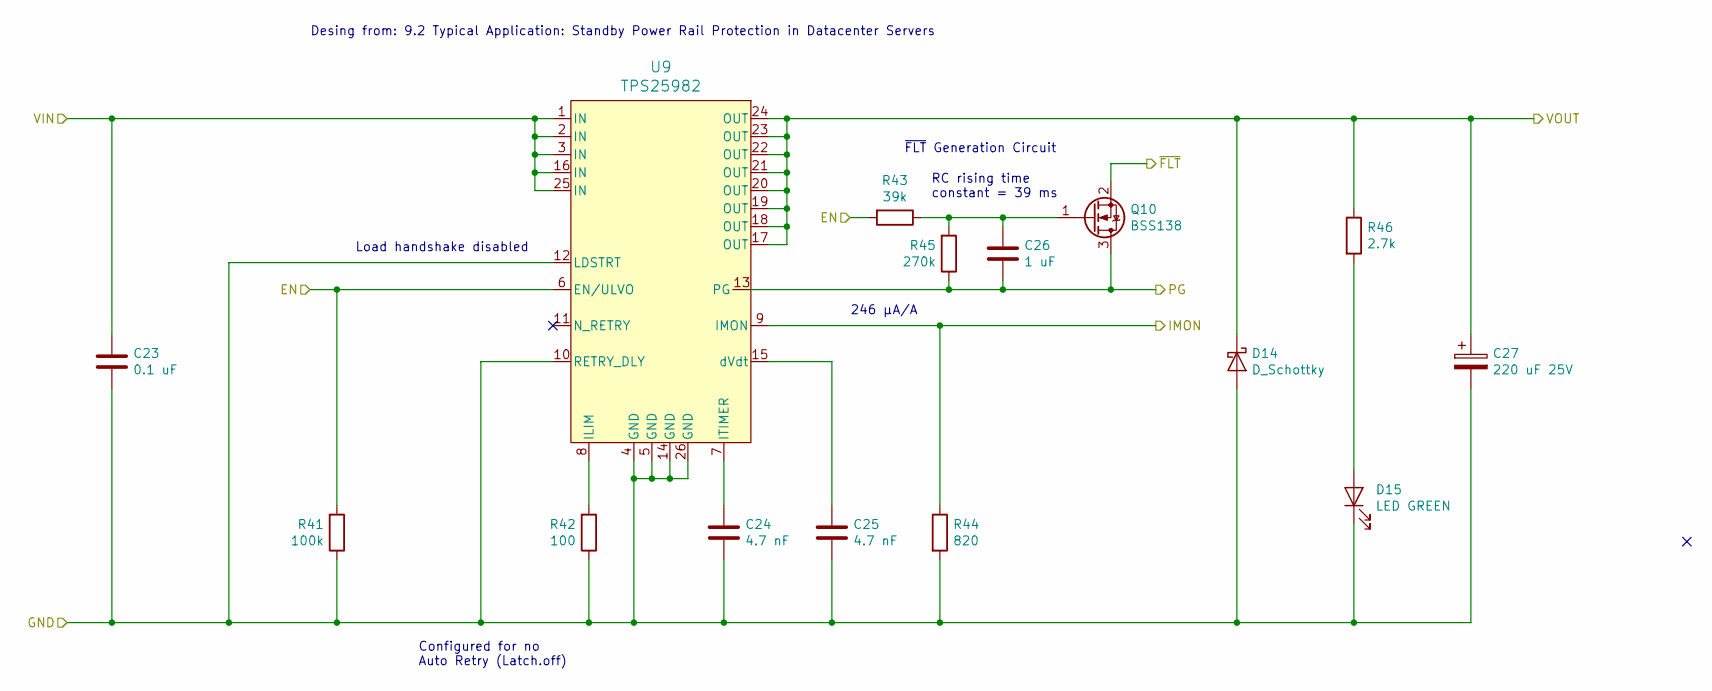
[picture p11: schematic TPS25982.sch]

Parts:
C13: 0.1 uF; C_0603_1608Metric
C14, C15: 4.7 nF; C_0603_1608Metric
C16: 1 uF; C_0603_1608Metric
C17: 220 uF 25V; CP_Radial_D8.0mm_P3.50mm; MPN ESE227M025AG3AA
D10: D_Schottky; D_SOD-123; MPN 1N5819HW
D15: LED GREEN; LED_0603_1608Metric
Q8: BSS138; SOT-23
R29: 100k; R_0603_1608Metric
R30: 100; R_0603_1608Metric
R31: 39k; R_0603_1608Metric
R32: 820; R_0603_1608Metric
R33: 270k; R_0603_1608Metric
R46: 2.7k; R_0603_1608Metric
U7: TPS25982; TPS259824ONRGET; MPN TPS259824ONRGET

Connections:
+12VA: C13.2, U7.1 (IN), U7.2 (IN), U7.3 (IN), U7.16 (IN), U7.25 (IN); also elsewhere on the board
/DB_INT_AUTO_EN: R29.2, R31.2, U7.6 (EN/ULVO); also elsewhere on the board
/DB_INT_AUTO_IMON: R32.1, U7.9 (IMON); also elsewhere on the board
/DB_INT_AUTO_PG: C16.1, Q8.3 (D), R33.1, U7.13 (PG); also elsewhere on the board
/eFuse_~FLT: Q8.2 (S); also elsewhere on the board
GND: C13.1, C14.2, C15.2, C17.2, D10.2 (A), D15.1 (K), R29.1, R30.1, R32.2, U7.4 (GND), U7.5 (GND), U7.10 (RETRY_DLY), U7.12 (LDSTRT), U7.14 (GND), U7.26 (GND); also elsewhere on the board
unnamed: C14.1, U7.7 (ITIMER)
unnamed: C15.1, U7.15 (dVdt)
unnamed: C16.2, Q8.1 (G), R31.1, R33.2
unnamed: D15.2 (A), R46.2
unnamed: R30.2, U7.8 (ILIM)

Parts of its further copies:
C18, C23: 0.1 uF; C_0603_1608Metric
C19, C20, C24, C25: 4.7 nF; C_0603_1608Metric
C21, C26: 1 uF; C_0603_1608Metric
C22, C27: 220 uF 25V; CP_Radial_D8.0mm_P3.50mm; MPN ESE227M025AG3AA
D11, D13: LED GREEN; LED_0603_1608Metric
D12, D14: D_Schottky; D_SOD-123; MPN 1N5819HW
Q9, Q10: BSS138; SOT-23
R34, R40: 2.7k; R_0603_1608Metric
R35, R41: 100k; R_0603_1608Metric
R36, R42: 100; R_0603_1608Metric
R37, R43: 39k; R_0603_1608Metric
R38, R44: 820; R_0603_1608Metric
R39, R45: 270k; R_0603_1608Metric
U8, U9: TPS25982; TPS259824ONRGET; MPN TPS259824ONRGET

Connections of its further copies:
+12V: C18.2, C23.2, U8.1 (IN), U8.2 (IN), U8.3 (IN), U8.16 (IN), U8.25 (IN), U9.1 (IN), U9.2 (IN), U9.3 (IN), U9.16 (IN), U9.25 (IN); also elsewhere on the board
/ACU_12V: C22.1, D12.1 (K), R40.1, U8.17 (OUT), U8.18 (OUT), U8.19 (OUT), U8.20 (OUT), U8.21 (OUT), U8.22 (OUT), U8.23 (OUT), U8.24 (OUT); also elsewhere on the board
/ACU_EN: R35.2, R37.2, U8.6 (EN/ULVO); also elsewhere on the board
/ACU_IMON: R38.1, U8.9 (IMON); also elsewhere on the board
/ACU_PG: C21.1, Q9.3 (D), R39.1, U8.13 (PG); also elsewhere on the board
/DB_EXT_EN: R41.2, R43.2, U9.6 (EN/ULVO); also elsewhere on the board
/DB_EXT_IMON: R44.1, U9.9 (IMON); also elsewhere on the board
/DB_EXT_PG: C26.1, Q10.3 (D), R45.1, U9.13 (PG); also elsewhere on the board
/eFuse_~FLT: Q9.2 (S), Q10.2 (S); also elsewhere on the board
GND: C18.1, C19.2, C20.2, C22.2, C23.1, C24.2, C25.2, C27.2, D11.1 (K), D12.2 (A), D13.1 (K), D14.2 (A), R35.1, R36.1, R38.2, R41.1, R42.1, R44.2, U8.4 (GND), U8.5 (GND), U8.10 (RETRY_DLY), U8.12 (LDSTRT), U8.14 (GND), U8.26 (GND), U9.4 (GND), U9.5 (GND), U9.10 (RETRY_DLY), U9.12 (LDSTRT), U9.14 (GND), U9.26 (GND); also elsewhere on the board
unnamed: C19.1, U8.7 (ITIMER)
unnamed: C20.1, U8.15 (dVdt)
unnamed: C21.2, Q9.1 (G), R37.1, R39.2
unnamed: C24.1, U9.7 (ITIMER)
unnamed: C25.1, U9.15 (dVdt)
unnamed: C26.2, Q10.1 (G), R43.1, R45.2
unnamed: D11.2 (A), R34.2
unnamed: D13.2 (A), R40.2
unnamed: R36.2, U8.8 (ILIM)
unnamed: R42.2, U9.8 (ILIM)

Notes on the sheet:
246 µA/A
Load handshake disabled
Configured for no Auto Retry (Latch.off)
Desing from: 9.2 Typical Application: Standby Power Rail Protection in Datacenter Servers
RC rising time constant = 39 ms
~FLT~ Generation Circuit

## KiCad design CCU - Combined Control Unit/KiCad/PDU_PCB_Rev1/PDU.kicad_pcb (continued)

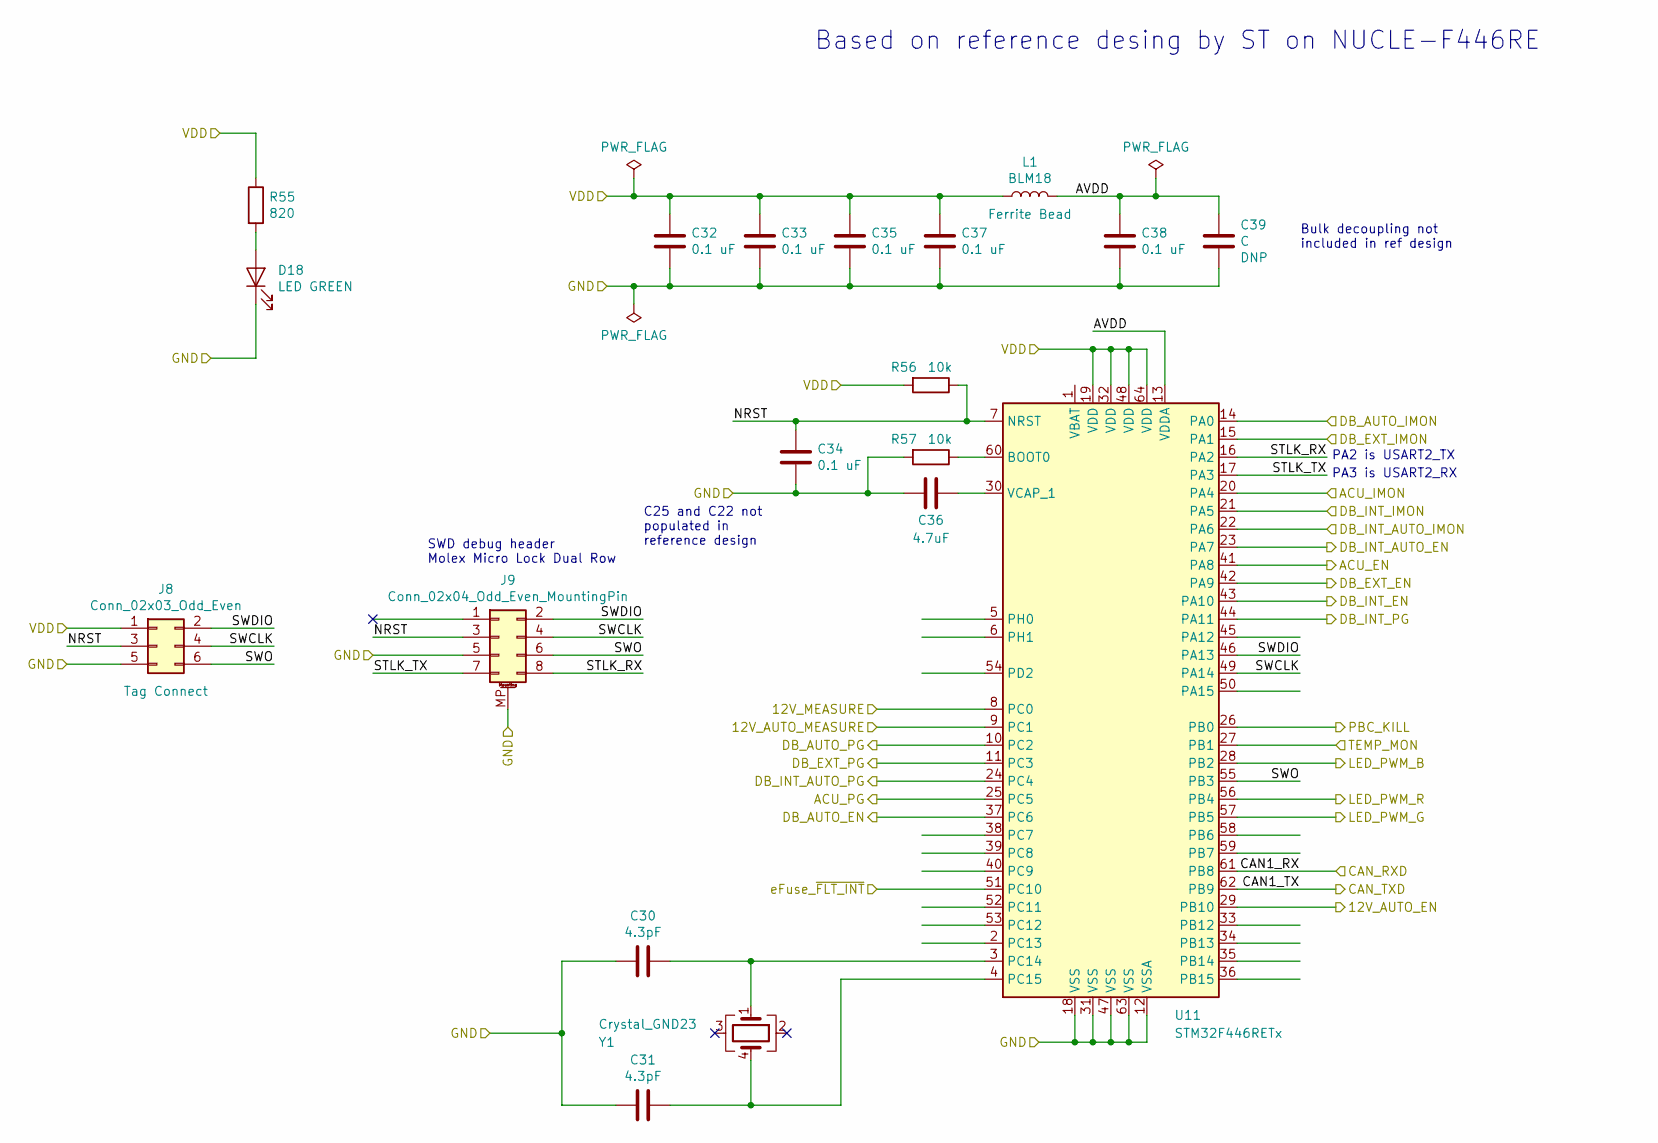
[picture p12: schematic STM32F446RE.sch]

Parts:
C30, C31: 4.3pF; C_0603_1608Metric
C32, C33, C34, C35, C37, C38: 0.1 uF; C_0603_1608Metric
C36: 4.7uF; C_0603_1608Metric
C39: C; C_0603_1608Metric
D18: LED GREEN; LED_0603_1608Metric
J8: Conn_02x03_Odd_Even; Tag-Connect_TC2030-IDC-NL_2x03_P1.27mm_Vertical
J9: Conn_02x04_Odd_Even_MountingPin; Molex_Micro-Lock_5054330871_2x4_P1.25_Vertical; MPN 538-505433-0871
L1: BLM18; L_0603_1608Metric; MPN BLM18PG471SN1D
R55: 820; R_0603_1608Metric
R56, R57: 10k; R_0603_1608Metric
U11: STM32F446RETx; LQFP-64_10x10mm_P0.5mm
Y1: Crystal_GND23; Crystal_SMD_Abracon_ABS25-4Pin_8.0x3.8mm; MPN ABS25-32.768KHZ-6-T

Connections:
+3V3: C32.1, C33.1, C35.1, C37.1, J8.1, L1.1, R55.1, R56.2, U11.19 (VDD), U11.32 (VDD), U11.48 (VDD), U11.64 (VDD); also elsewhere on the board
/12V_AUTO_EN: U11.29 (PB10); also elsewhere on the board
/12V_AUTO_MEASURE: U11.9 (PC1); also elsewhere on the board
/12V_MEASURE: U11.8 (PC0); also elsewhere on the board
/ACU_EN: U11.41 (PA8); also elsewhere on the board
/ACU_IMON: U11.20 (PA4); also elsewhere on the board
/ACU_PG: U11.25 (PC5); also elsewhere on the board
/DB_AUTO_EN: U11.37 (PC6); also elsewhere on the board
/DB_AUTO_IMON: U11.14 (PA0); also elsewhere on the board
/DB_AUTO_PG: U11.10 (PC2); also elsewhere on the board
/DB_EXT_EN: U11.42 (PA9); also elsewhere on the board
/DB_EXT_IMON: U11.15 (PA1); also elsewhere on the board
/DB_EXT_PG: U11.11 (PC3); also elsewhere on the board
/DB_INT_AUTO_EN: U11.23 (PA7); also elsewhere on the board
/DB_INT_AUTO_IMON: U11.22 (PA6); also elsewhere on the board
/DB_INT_AUTO_PG: U11.24 (PC4); also elsewhere on the board
/DB_INT_EN: U11.43 (PA10); also elsewhere on the board
/DB_INT_IMON: U11.21 (PA5); also elsewhere on the board
/DB_INT_PG: U11.44 (PA11); also elsewhere on the board
/PBC_KILL: U11.26 (PB0); also elsewhere on the board
/STM32F446RE/AVDD: C38.1, C39.1, L1.2, U11.13 (VDDA)
/STM32F446RE/CAN_RXD: U11.61 (PB8); also elsewhere on the board
/STM32F446RE/CAN_TXD: U11.62 (PB9); also elsewhere on the board
/STM32F446RE/NRST: C34.1, J8.3, J9.3, R56.1, U11.7 (NRST)
/STM32F446RE/STLK_RX: J9.8, U11.16 (PA2)
/STM32F446RE/STLK_TX: J9.7, U11.17 (PA3)
/STM32F446RE/SWCLK: J8.4, J9.4, U11.49 (PA14)
/STM32F446RE/SWDIO: J8.2, J9.2, U11.46 (PA13)
/STM32F446RE/SWO: J8.6, J9.6, U11.55 (PB3)
/S_LED_B_A: U11.28 (PB2); also elsewhere on the board
/S_LED_G_A: U11.57 (PB5); also elsewhere on the board
/S_LED_R_A: U11.56 (PB4); also elsewhere on the board
/TEMP_MON: U11.27 (PB1); also elsewhere on the board
/eFuse_~FLT: U11.51 (PC10); also elsewhere on the board
GND: C30.2, C31.2, C32.2, C33.2, C34.2, C35.2, C36.2, C37.2, C38.2, C39.2, D18.1 (K), J8.5, J9.5, J9.MP (MountPin), R57.2, U11.12 (VSSA), U11.18 (VSS), U11.31 (VSS), U11.47 (VSS), U11.63 (VSS); also elsewhere on the board
unnamed: C30.1, U11.3 (PC14), Y1.1
unnamed: C31.1, U11.4 (PC15), Y1.4
unnamed: C36.1, U11.30 (VCAP_1)
unnamed: D18.2 (A), R55.2
unnamed: R57.1, U11.60 (BOOT0)

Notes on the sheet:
C25 and C22 not populated in reference design
SWD debug header Molex Micro Lock Dual Row
Based on reference desing by ST on NUCLE-F446RE
PA3 is USART2_RX
PA2 is USART2_TX
Bulk decoupling not included in ref design

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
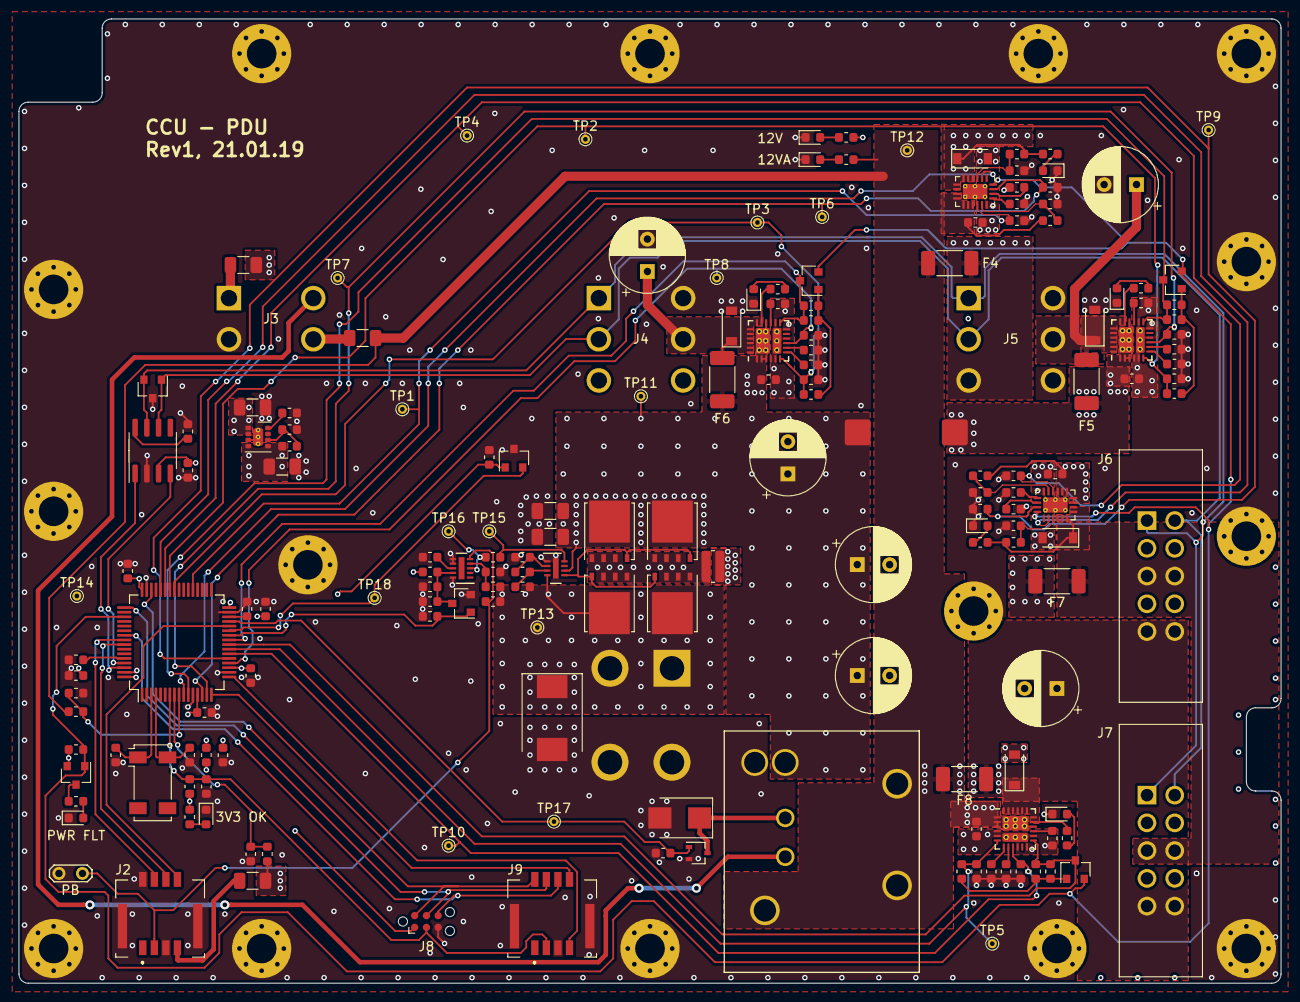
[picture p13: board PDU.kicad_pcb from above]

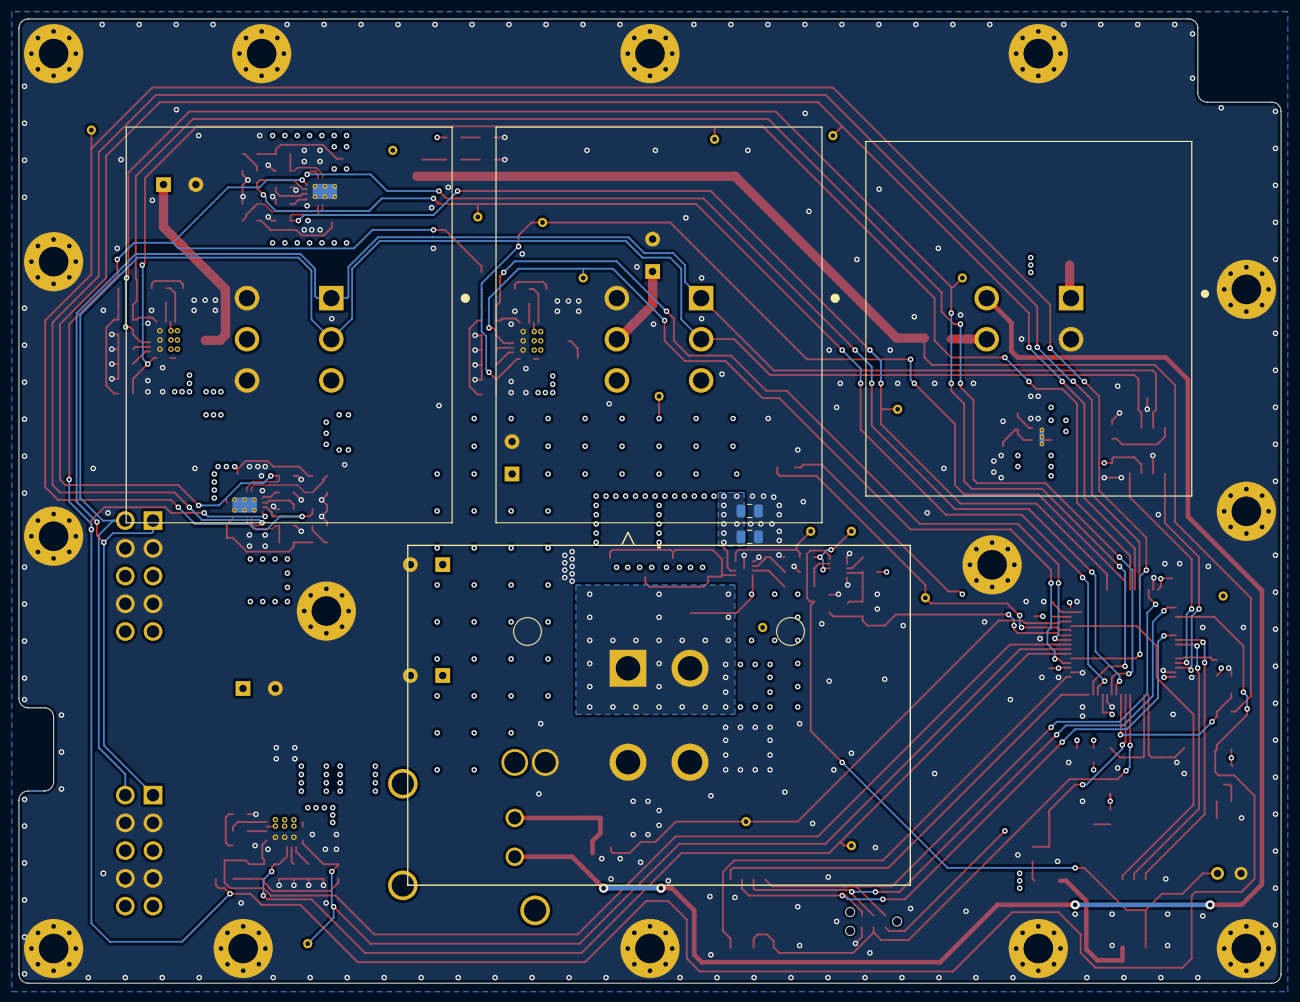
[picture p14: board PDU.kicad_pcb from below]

Board: 4 copper layers, 136.5 x 104.3 mm, 196 parts (6 on the bottom side), 97 nets.

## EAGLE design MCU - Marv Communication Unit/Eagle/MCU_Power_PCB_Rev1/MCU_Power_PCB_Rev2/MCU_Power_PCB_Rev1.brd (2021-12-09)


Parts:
C3, C6: 0.1 uF; C0603
C4, C5: 0.033 uF; C0603
D1, D2, D3, D4, D5: LED5MM
D6: 1.8V; SOD-123_MINI-SMA
D7, D8, D9: 6.0V; SOD-123_MINI-SMA
D10: 10.0V; SOD-123_MINI-SMA
D11: 12.00V; SOD-123_MINI-SMA
D12: 2.5V; SOD-123_MINI-SMA
D13: 3.3V; SOD-123_MINI-SMA
HOLE1, HOLE2, HOLE3, HOLE4: M3_MOUNTING_HOLE
IC1: LTC2950ITS8-2#TRMPBF; SOT65P280X100-8N
J1, J2: 39-30-3035; 39303035
J3: 39-30-3046; 39303046
J4, J5: 3522-2; 35222
J6, J7, J8, J9: 39-30-0020; 39-30-1020_1
Q1, Q4: IPD90P03P4-04; PG-TO252-3-11
Q6: 2N7002PW,115; SOT323
R1, R2, R3, R4, R5: 1K; R0603
R9: 360K 0.1%; R0603
R10, R11: 100K; R0603
R12: 24K 0.1%; R0603
S1: SKHHA/D

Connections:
+12V: C3.1, D11.C, IC1.1 (VIN), J4.2, J4.4, Q1.2 (S), Q4.2 (S), S1.1, S1.2
GND: C3.2, C4.2, C5.2, C6.2, D1.K, D2.K, D3.K, D4.K, D5.K, IC1.4 (GND), J1.1, J2.1, J3.2, J3.4, J6.1, J7.1, J8.1, J9.1, Q6.2 (S), R10.2, R11.2, R12.2
unnamed: J5.1, J5.3, Q4.3 (D)
unnamed: C4.1, IC1.3 (ONT)
unnamed: D2.A, R2.1
unnamed: D7.A, Q6.1 (G), R2.2, R11.1
unnamed: D8.A, R3.2
unnamed: D9.A, R4.2
unnamed: D10.A, R5.2
unnamed: D3.A, R3.1
unnamed: D4.A, R4.1
unnamed: D5.A, R5.1
unnamed: IC1.2 (!PB), J3.3
unnamed: D1.A, Q6.3 (D), R1.2
unnamed: J2.2, J4.1, J4.3
unnamed: D6.A, D7.C
unnamed: D6.C, D10.C, D12.C, D13.C, R1.1, S1.3, S1.4
unnamed: C5.1, IC1.7 (OFFT)
unnamed: J1.3, J5.2, J5.4
unnamed: D8.C, D12.A
unnamed: D11.A, Q4.1 (G), R10.1
unnamed: D9.C, D13.A
unnamed: C6.1, IC1.5 (!INT), IC1.8 (!KILL), R9.2, R12.1
unnamed: IC1.6 (EN/!EN), Q1.1 (G)
VCC: J3.1, J6.2, J7.2, J8.2, J9.2, Q1.3 (D), R9.1

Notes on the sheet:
Charging port
Battery port
Power out - 4
Power out - 3
Power out - 2
Power out - 1
Battery port fuse - 7.5A
Should cut power at ~9.9V IC cuts power under 0.6V !KILL
1. LED+ 2. LED- 3. PB+ 4. PB-
Charging port fuse - 7.5A
1. GND 2. 12V 3. NC
1. GND 2. NC 3. 12V
1. GND 2. VCC
Battery status LEDs
Power input/output, fuses
Pushbutton controller/voltage monitor
Mounting holes
Viktor Lindström
CHALMERS
~12.2V
~11.6V
~10.0V
~10.7V



Board: 2 copper layers, 100.0 x 50.0 mm, 44 parts (34 on the bottom side), 25 nets.

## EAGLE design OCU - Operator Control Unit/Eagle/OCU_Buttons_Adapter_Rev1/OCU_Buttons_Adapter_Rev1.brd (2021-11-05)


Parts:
H1, H2: S8131-46R; S813146R
J1, J2, J3, J4: 1053091202; 1053091402
J5, J6: 505567-0271; 5055680271
J7: 505567-0371; 5055680371
R1, R2, R3: 2K; R0603

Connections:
GND: H1.1, H2.1, J5.MP1, J5.MP2, J6.MP1, J6.MP2, J7.2, J7.MP1, J7.MP2, R3.1
unnamed: J1.1, J5.1
unnamed: J1.2, J5.2
unnamed: J2.1, J6.1
unnamed: J2.2, J6.2
unnamed: J3.1, R1.1, R2.2
unnamed: J4.1, R2.1, R3.2
unnamed: J3.2, J4.2, J7.3
unnamed: J7.1, R1.2

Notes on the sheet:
Green button
Red button
Up button ~3.3V level => ~2.18V after voltage divider
Down button ~1.67V level => ~1.1V after voltage divider
Two buttons to single analogue input
1. 5V 2. GND 3. SIG


Board: 2 copper layers, 32.0 x 69.7 mm, 12 parts (0 on the bottom side), 9 nets.

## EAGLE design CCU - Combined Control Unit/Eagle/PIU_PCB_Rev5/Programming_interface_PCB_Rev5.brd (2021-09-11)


Board: 4 copper layers, 95.0 x 52.1 mm, 165 parts (0 on the bottom side), 117 nets.

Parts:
330R: 1K1; R0603
C1, C19: 4Pf?; C0603
C2, C4, C17, C18, C20, C24, C25, C26, C28, C30, C31: 0.1uF; C0603
C3: 10uF; C0603
C5, C6: 33pF; C0603
C7, C8, C9, C10, C11, C12, C13, C14, C15, C16: 22pF; C0603
C21, C22, C23, C27: 1uF; C0603
C29: 100uF; PANASONIC_C
D1, D2: CHIP-LED0805
F1: OZCJ0050; OZCJ
FP1, FP2: R0603
IC1: TUSB2046IBVFR; QFP80P900X900X160-32N
IC2: SN75240PW; SOP65P640X120-8N
IC3: CP2108-B03-GM; QFN50P900X900X90-65N
J1: 505568-0571; 5055680571
J2: 505567-0371; 5055680371
Q1: BC817; SOT23
Q2, Q3, Q4: 2N7002PW,115; SOT323
Q5, Q6: BSS223PW; SOT323
R1: 1K6; R0603
R2: 22; R0805
R3: 1K5; R0805
R4: 15K; R0603
R5, R8: 1K5; R0603
R6, R7: 27; R0603
R9, R12: 100K; R0603
R10, R11, R13, R14: 10K; R0603
RN1, RN2: CAY16-27R0F4LF; CAY16-J4
RN3, RN4: CAY16-1502F4LF; CAY16-J4
ST_LINK1:C19, ST_LINK1:C22, ST_LINK1:C23, ST_LINK1:C24: 0.1uF; C0603
ST_LINK1:C20, ST_LINK1:C21: 10pF; C0603
ST_LINK1:D1, ST_LINK1:D2: CHIP-LED0805
ST_LINK1:IC3: STM32F103CBT6TR; QFP50P900X900X160-48N
ST_LINK1:Q2: BC817; SOT23
ST_LINK1:R1: 0; R0603
ST_LINK1:R2, ST_LINK1:R3: 330; R0603
ST_LINK1:R25: 1K5; R0603
ST_LINK1:R26, ST_LINK1:R32: 10K; R0603
ST_LINK1:R27: 36K; R0603
ST_LINK1:R28: 100; R0603
ST_LINK1:R29, ST_LINK1:R33: 100K; R0603
ST_LINK1:R30, ST_LINK1:R34, ST_LINK1:R35: 4K7; R0603
ST_LINK1:R31: 2K7; R0603
ST_LINK1:R36: 100; R0805
ST_LINK1:SWD1: SWD_TAGCONNECTNO-LEG; TC2030-IDC-NL
ST_LINK1:Y2: NX3225GD-8MHZ-STD-CRA-3; RESC3226X100N
SWD1: SWD_TAGCONNECTNO-LEG; TC2030-IDC-NL
SWITCH_UNIT1:C1, SWITCH_UNIT2:C1, SWITCH_UNIT3:C1, SWITCH_UNIT4:C1: 0.1uF; C0603
SWITCH_UNIT1:D1, SWITCH_UNIT2:D1, SWITCH_UNIT3:D1, SWITCH_UNIT4:D1: CHIP-LED0805
SWITCH_UNIT1:J2, SWITCH_UNIT2:J2, SWITCH_UNIT3:J2, SWITCH_UNIT4:J2: 505433-0871; 5054330871
SWITCH_UNIT1:Q1, SWITCH_UNIT1:Q2, SWITCH_UNIT1:Q3, SWITCH_UNIT1:Q5, SWITCH_UNIT2:Q1, SWITCH_UNIT2:Q2, SWITCH_UNIT2:Q3, SWITCH_UNIT2:Q5, SWITCH_UNIT3:Q1, SWITCH_UNIT3:Q2, SWITCH_UNIT3:Q3, SWITCH_UNIT3:Q5, SWITCH_UNIT4:Q1, SWITCH_UNIT4:Q2, SWITCH_UNIT4:Q3, SWITCH_UNIT4:Q5: 2N7002PW,115; SOT323
SWITCH_UNIT1:R1, SWITCH_UNIT2:R1, SWITCH_UNIT3:R1, SWITCH_UNIT4:R1: 1K6; R0603
SWITCH_UNIT1:R2, SWITCH_UNIT2:R2, SWITCH_UNIT3:R2, SWITCH_UNIT4:R2: -; R0603
SWITCH_UNIT1:R3, SWITCH_UNIT2:R3, SWITCH_UNIT3:R3, SWITCH_UNIT4:R3: -; R0402
SWITCH_UNIT1:R4, SWITCH_UNIT1:R5, SWITCH_UNIT2:R4, SWITCH_UNIT2:R5, SWITCH_UNIT3:R4, SWITCH_UNIT3:R5, SWITCH_UNIT4:R4, SWITCH_UNIT4:R5: 1K; R0402
SWITCH_UNIT1:R6, SWITCH_UNIT2:R6, SWITCH_UNIT3:R6, SWITCH_UNIT4:R6: 0R; R0402
SWITCH_UNIT1:R11, SWITCH_UNIT2:R11, SWITCH_UNIT3:R11, SWITCH_UNIT4:R11: 10K; R0603
SWITCH_UNIT1:SW1, SWITCH_UNIT2:SW1, SWITCH_UNIT3:SW1, SWITCH_UNIT4:SW1: TMUX1309QBQBRQ1; QFN16-4X4
U1: LD1117S33TR; SOT230P700X180-4N
U$1, U$2, U$3, U$4, U$5, U$6, U$7: M3_MOUNTING_HOLE
U$8: SAMD21G18A-ARDUINO; TQFP48
U$9: ST2012SB32768H5KPWAA
Y1: ABMM-6.000MHZ-B2-T

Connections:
+3V3: 330R.1, C3.1, C17.1, C18.2, FP2.1, IC1.3, IC1.10, IC1.14, IC1.18, IC1.22, IC1.25, IC1.26, Q5.2, R2.2, R3.1, R10.2, R14.2, SWD1.1, SWITCH_UNIT1:R4.2, SWITCH_UNIT1:R5.2, SWITCH_UNIT2:R4.2, SWITCH_UNIT2:R5.2, SWITCH_UNIT3:R4.2, SWITCH_UNIT3:R5.2, SWITCH_UNIT4:R4.2, SWITCH_UNIT4:R5.2, U1.2, U1.4
+5V: C2.1, C22.1, C29.+, F1.1, IC3.60, IC3.61, Q6.2, R1.2, R4.2, R13.2, SWITCH_UNIT1:C1.1, SWITCH_UNIT1:R1.2, SWITCH_UNIT1:SW1.16, SWITCH_UNIT2:C1.1, SWITCH_UNIT2:R1.2, SWITCH_UNIT2:SW1.16, SWITCH_UNIT3:C1.1, SWITCH_UNIT3:R1.2, SWITCH_UNIT3:SW1.16, SWITCH_UNIT4:C1.1, SWITCH_UNIT4:R1.2, SWITCH_UNIT4:SW1.16, U1.3
D1_2_N: C11.1, IC1.11, RN1.7
D1_2_P: C12.1, IC1.12, RN1.5
D1_N: RN1.8, RN3.7, ST_LINK1:IC3.32
D1_P: RN1.6, RN3.5, ST_LINK1:IC3.33, ST_LINK1:R25.1
D2_2_N: C13.1, IC1.15, RN1.3
D2_2_P: C14.1, IC1.16, RN1.1
D2_N: RN1.4, RN3.3, U$8.33
D2_P: RN1.2, RN3.1, U$8.34
D3_2_N: C7.1, IC1.19, RN2.7
D3_2_P: C8.1, IC1.20, RN2.5
D3_N: IC3.63, RN2.8, RN4.7
D3_P: IC3.62, RN2.6, RN4.5
D4_2_N: C9.1, IC1.23, RN2.3
D4_2_P: C10.1, IC1.24, RN2.1
D4_N: J2.3, RN2.4, RN4.3
D4_P: J2.2, RN2.2, RN4.1
GND: C1.1, C2.2, C3.2, C4.2, C5.2, C6.2, C7.2, C8.2, C9.2, C10.2, C11.2, C12.2, C13.2, C14.2, C15.1, C16.1, C17.2, C18.1, C19.1, C20.1, C21.2, C22.2, C23.2, C24.2, C25.2, C26.2, C27.2, C28.2, C29.-, C30.2, C31.1, D1.C, FP1.2, IC1.7, IC1.8, IC1.27, IC1.28, IC1.31, IC2.1, IC2.3, IC3.2, IC3.25, IC3.59, IC3.65, J1.4, J1.MP1, J1.MP2, J2.1, J2.MP1, J2.MP2, Q2.2, Q3.2, Q4.2, R9.1, R11.1, RN3.2, RN3.4, RN3.6, RN3.8, RN4.2, RN4.4, RN4.6, RN4.8, ST_LINK1:C19.1, ST_LINK1:C20.1, ST_LINK1:C21.1, ST_LINK1:C22.1, ST_LINK1:C23.2, ST_LINK1:C24.2, ST_LINK1:D1.C, ST_LINK1:IC3.8, ST_LINK1:IC3.20, ST_LINK1:IC3.23, ST_LINK1:IC3.35, ST_LINK1:IC3.47, ST_LINK1:R27.1, ST_LINK1:R29.2, ST_LINK1:R30.2, ST_LINK1:R32.2, ST_LINK1:R35.1, ST_LINK1:SWD1.5, SWD1.5, SWITCH_UNIT1:C1.2, SWITCH_UNIT1:J2.5, SWITCH_UNIT1:J2.MP1, SWITCH_UNIT1:J2.MP2, SWITCH_UNIT1:Q1.2, SWITCH_UNIT1:Q2.2, SWITCH_UNIT1:Q3.2, SWITCH_UNIT1:R2.1, SWITCH_UNIT1:R11.2, SWITCH_UNIT1:SW1.8, SWITCH_UNIT1:SW1.9, SWITCH_UNIT1:SW1.10, SWITCH_UNIT1:SW1.EXP, SWITCH_UNIT1:SW1.P$1, SWITCH_UNIT1:SW1.P$2, SWITCH_UNIT1:SW1.P$3, SWITCH_UNIT2:C1.2, SWITCH_UNIT2:J2.5, SWITCH_UNIT2:J2.MP1, SWITCH_UNIT2:J2.MP2, SWITCH_UNIT2:Q1.2, SWITCH_UNIT2:Q2.2, SWITCH_UNIT2:Q3.2, SWITCH_UNIT2:R2.1, SWITCH_UNIT2:R11.2, SWITCH_UNIT2:SW1.8, SWITCH_UNIT2:SW1.9, SWITCH_UNIT2:SW1.10, SWITCH_UNIT2:SW1.EXP, SWITCH_UNIT2:SW1.P$1, SWITCH_UNIT2:SW1.P$2, SWITCH_UNIT2:SW1.P$3, SWITCH_UNIT3:C1.2, SWITCH_UNIT3:J2.5, SWITCH_UNIT3:J2.MP1, SWITCH_UNIT3:J2.MP2, SWITCH_UNIT3:Q1.2, SWITCH_UNIT3:Q2.2, SWITCH_UNIT3:Q3.2, SWITCH_UNIT3:R2.1, SWITCH_UNIT3:R11.2, SWITCH_UNIT3:SW1.8, SWITCH_UNIT3:SW1.9, SWITCH_UNIT3:SW1.10, SWITCH_UNIT3:SW1.EXP, SWITCH_UNIT3:SW1.P$1, SWITCH_UNIT3:SW1.P$2, SWITCH_UNIT3:SW1.P$3, SWITCH_UNIT4:C1.2, SWITCH_UNIT4:J2.5, SWITCH_UNIT4:J2.MP1, SWITCH_UNIT4:J2.MP2, SWITCH_UNIT4:Q1.2, SWITCH_UNIT4:Q2.2, SWITCH_UNIT4:Q3.2, SWITCH_UNIT4:R2.1, SWITCH_UNIT4:R11.2, SWITCH_UNIT4:SW1.8, SWITCH_UNIT4:SW1.9, SWITCH_UNIT4:SW1.10, SWITCH_UNIT4:SW1.EXP, SWITCH_UNIT4:SW1.P$1, SWITCH_UNIT4:SW1.P$2, SWITCH_UNIT4:SW1.P$3, U1.1, U$8.5, U$8.18, U$8.35, U$8.42
unnamed: C4.1, IC1.4, Q1.3, R2.1, R3.2
unnamed: FP1.1, J1.5
unnamed: Q1.1, R4.1
unnamed: Q1.2, R5.1
unnamed: Q4.3, Q5.1, R14.1
unnamed: Q3.3, Q6.1, R13.1
unnamed: D1.A, R1.1
unnamed: C20.2, C31.2, FP2.2, U$8.6, U$8.17, U$8.36, U$8.44
unnamed: C1.2, U$8.1, U$9.P$2
unnamed: IC1.29, R8.1
unnamed: C6.1, IC1.30, Y1.3
unnamed: C5.1, R8.2, Y1.1
unnamed: C19.2, U$8.2, U$9.P$1
unnamed: SWD1.2, U$8.46
unnamed: C30.1, R10.1, SWD1.3, U$8.40
unnamed: SWD1.4, U$8.45
unnamed: C21.1, U$8.43
unnamed: 330R.2, D2.A
unnamed: IC3.64, R12.1
unnamed: D2.C, Q2.3
unnamed: Q6.3, ST_LINK1:R26.2, ST_LINK1:R31.1
unnamed: Q2.1, R11.2, U$8.26
unnamed: Q5.3, ST_LINK1:C19.2, ST_LINK1:C23.1, ST_LINK1:C24.1, ST_LINK1:D2.A, ST_LINK1:IC3.1, ST_LINK1:IC3.9, ST_LINK1:IC3.24, ST_LINK1:IC3.36, ST_LINK1:IC3.48, ST_LINK1:Q2.3, ST_LINK1:R33.2, ST_LINK1:R34.1, ST_LINK1:SWD1.1
unnamed: F1.2, J1.1
NCU_NRST_ON: SWITCH_UNIT1:Q1.1, SWITCH_UNIT1:Q5.1, SWITCH_UNIT1:R2.2, SWITCH_UNIT1:R11.1, U$8.14
NCU_ON: SWITCH_UNIT1:SW1.6, U$8.30
PDU_NRST_ON: SWITCH_UNIT4:Q1.1, SWITCH_UNIT4:Q5.1, SWITCH_UNIT4:R2.2, SWITCH_UNIT4:R11.1, U$8.23
PDU_ON: SWITCH_UNIT4:SW1.6, U$8.27
RX_NCU: IC3.56, SWITCH_UNIT1:Q3.3, SWITCH_UNIT1:R3.2, SWITCH_UNIT1:R5.1
RX_PDU: IC3.1, SWITCH_UNIT4:Q3.3, SWITCH_UNIT4:R3.2, SWITCH_UNIT4:R5.1
RX_TCU: IC3.15, SWITCH_UNIT3:Q3.3, SWITCH_UNIT3:R3.2, SWITCH_UNIT3:R5.1
RX_UCU: IC3.48, SWITCH_UNIT2:Q3.3, SWITCH_UNIT2:R3.2, SWITCH_UNIT2:R5.1
ST_LINK1:N$1: ST_LINK1:D1.A, ST_LINK1:R2.1
ST_LINK1:N$3: ST_LINK1:D2.C, ST_LINK1:R3.1
ST_LINK1:N$7: ST_LINK1:Q2.2, ST_LINK1:R25.2
ST_LINK1:N$8: ST_LINK1:Q2.1, ST_LINK1:R26.1, ST_LINK1:R27.2, ST_LINK1:R28.2
ST_LINK1:N$15: ST_LINK1:IC3.39, ST_LINK1:R30.1, ST_LINK1:R31.2
ST_LINK1:N$16: ST_LINK1:IC3.2, ST_LINK1:R32.1
ST_LINK1:N$21: ST_LINK1:IC3.44, ST_LINK1:R29.1
ST_LINK1:N$22: ST_LINK1:C20.2, ST_LINK1:IC3.5, ST_LINK1:Y2.1
ST_LINK1:N$23: ST_LINK1:IC3.10, ST_LINK1:R34.2, ST_LINK1:R35.2
ST_LINK1:N$24: ST_LINK1:C21.2, ST_LINK1:IC3.6, ST_LINK1:Y2.2
ST_LINK1:N$25: ST_LINK1:C22.2, ST_LINK1:IC3.7, ST_LINK1:R1.1, ST_LINK1:R33.1
ST_LINK1:N$26: ST_LINK1:IC3.25, ST_LINK1:R36.2
ST_LINK1:STLK_LED: ST_LINK1:IC3.30, ST_LINK1:R2.2, ST_LINK1:R3.2
ST_LINK1:STM_NRST: ST_LINK1:R1.2, ST_LINK1:SWD1.3
ST_LINK1:STM_SWCLK: ST_LINK1:IC3.37, ST_LINK1:SWD1.4
ST_LINK1:STM_SWDIO: ST_LINK1:IC3.34, ST_LINK1:SWD1.2
ST_LINK1:USB_RENUM: ST_LINK1:IC3.38, ST_LINK1:R28.1
ST_LINK_EN: Q3.1, Q4.1, R9.2, U$8.13
ST_LINK_NRST_OUT: ST_LINK1:IC3.18, SWITCH_UNIT1:Q5.2, SWITCH_UNIT2:Q5.2, SWITCH_UNIT3:Q5.2, SWITCH_UNIT4:Q5.2
ST_LINK_SWDCLK_OUT: ST_LINK1:IC3.15, ST_LINK1:IC3.26, SWITCH_UNIT1:SW1.12, SWITCH_UNIT2:SW1.12, SWITCH_UNIT3:SW1.12, SWITCH_UNIT4:SW1.12
ST_LINK_SWDIO_OUT: ST_LINK1:IC3.27, ST_LINK1:R36.1, SWITCH_UNIT1:SW1.1, SWITCH_UNIT2:SW1.1, SWITCH_UNIT3:SW1.1, SWITCH_UNIT4:SW1.1
SWITCH_UNIT1:N$2: SWITCH_UNIT1:D1.C, SWITCH_UNIT1:Q1.3
SWITCH_UNIT1:N$3: SWITCH_UNIT1:D1.A, SWITCH_UNIT1:R1.1
SWITCH_UNIT1:N$4: SWITCH_UNIT1:Q2.3, SWITCH_UNIT1:Q3.1, SWITCH_UNIT1:R4.1
SWITCH_UNIT1:RX_STM32: SWITCH_UNIT1:J2.7, SWITCH_UNIT1:R6.1
SWITCH_UNIT1:TX_STM32: SWITCH_UNIT1:J2.8, SWITCH_UNIT1:Q2.1, SWITCH_UNIT1:R3.1
SWITCH_UNIT1:UNIT_NRST: SWITCH_UNIT1:J2.3, SWITCH_UNIT1:Q5.3
SWITCH_UNIT1:UNIT_SWCLK: SWITCH_UNIT1:J2.4, SWITCH_UNIT1:SW1.13
SWITCH_UNIT1:UNIT_SWDIO: SWITCH_UNIT1:J2.2, SWITCH_UNIT1:SW1.3
SWITCH_UNIT2:N$2: SWITCH_UNIT2:D1.C, SWITCH_UNIT2:Q1.3
SWITCH_UNIT2:N$3: SWITCH_UNIT2:D1.A, SWITCH_UNIT2:R1.1
SWITCH_UNIT2:N$4: SWITCH_UNIT2:Q2.3, SWITCH_UNIT2:Q3.1, SWITCH_UNIT2:R4.1
SWITCH_UNIT2:RX_STM32: SWITCH_UNIT2:J2.7, SWITCH_UNIT2:R6.1
SWITCH_UNIT2:TX_STM32: SWITCH_UNIT2:J2.8, SWITCH_UNIT2:Q2.1, SWITCH_UNIT2:R3.1
SWITCH_UNIT2:UNIT_NRST: SWITCH_UNIT2:J2.3, SWITCH_UNIT2:Q5.3
SWITCH_UNIT2:UNIT_SWCLK: SWITCH_UNIT2:J2.4, SWITCH_UNIT2:SW1.13
SWITCH_UNIT2:UNIT_SWDIO: SWITCH_UNIT2:J2.2, SWITCH_UNIT2:SW1.3
SWITCH_UNIT3:N$2: SWITCH_UNIT3:D1.C, SWITCH_UNIT3:Q1.3
SWITCH_UNIT3:N$3: SWITCH_UNIT3:D1.A, SWITCH_UNIT3:R1.1
SWITCH_UNIT3:N$4: SWITCH_UNIT3:Q2.3, SWITCH_UNIT3:Q3.1, SWITCH_UNIT3:R4.1
SWITCH_UNIT3:RX_STM32: SWITCH_UNIT3:J2.7, SWITCH_UNIT3:R6.1
SWITCH_UNIT3:TX_STM32: SWITCH_UNIT3:J2.8, SWITCH_UNIT3:Q2.1, SWITCH_UNIT3:R3.1
SWITCH_UNIT3:UNIT_NRST: SWITCH_UNIT3:J2.3, SWITCH_UNIT3:Q5.3
SWITCH_UNIT3:UNIT_SWCLK: SWITCH_UNIT3:J2.4, SWITCH_UNIT3:SW1.13
SWITCH_UNIT3:UNIT_SWDIO: SWITCH_UNIT3:J2.2, SWITCH_UNIT3:SW1.3
SWITCH_UNIT4:N$2: SWITCH_UNIT4:D1.C, SWITCH_UNIT4:Q1.3
SWITCH_UNIT4:N$3: SWITCH_UNIT4:D1.A, SWITCH_UNIT4:R1.1
SWITCH_UNIT4:N$4: SWITCH_UNIT4:Q2.3, SWITCH_UNIT4:Q3.1, SWITCH_UNIT4:R4.1
SWITCH_UNIT4:RX_STM32: SWITCH_UNIT4:J2.7, SWITCH_UNIT4:R6.1
SWITCH_UNIT4:TX_STM32: SWITCH_UNIT4:J2.8, SWITCH_UNIT4:Q2.1, SWITCH_UNIT4:R3.1
SWITCH_UNIT4:UNIT_NRST: SWITCH_UNIT4:J2.3, SWITCH_UNIT4:Q5.3
SWITCH_UNIT4:UNIT_SWCLK: SWITCH_UNIT4:J2.4, SWITCH_UNIT4:SW1.13
SWITCH_UNIT4:UNIT_SWDIO: SWITCH_UNIT4:J2.2, SWITCH_UNIT4:SW1.3
TCU_NRST_ON: SWITCH_UNIT3:Q1.1, SWITCH_UNIT3:Q5.1, SWITCH_UNIT3:R2.2, SWITCH_UNIT3:R11.1, U$8.16
TCU_ON: SWITCH_UNIT3:SW1.6, U$8.28
TX_NCU: IC3.57, SWITCH_UNIT1:R6.2
TX_PDU: IC3.4, SWITCH_UNIT4:R6.2
TX_TCU: IC3.16, SWITCH_UNIT3:R6.2
TX_UCU: IC3.49, SWITCH_UNIT2:R6.2
UCU_NRST_ON: SWITCH_UNIT2:Q1.1, SWITCH_UNIT2:Q5.1, SWITCH_UNIT2:R2.2, SWITCH_UNIT2:R11.1, U$8.15
UCU_ON: SWITCH_UNIT2:SW1.6, U$8.29
USB_D1_N: C15.2, IC1.2, IC2.8, R6.1
USB_D1_P: C16.2, IC1.1, IC2.6, R7.1
USB_D2_N: J1.2, R6.2
USB_D2_P: J1.3, R5.2, R7.2
VIO: C23.1, C24.1, C25.1, C26.1, C27.1, C28.1, IC3.3, IC3.24, IC3.39, IC3.58, R12.2

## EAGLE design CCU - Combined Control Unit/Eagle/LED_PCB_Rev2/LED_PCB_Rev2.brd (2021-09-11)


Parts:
J1: 505568-0571; 5055680571
J2: 505433-0871; 5054330871
LED1: 150141M173100
Q1, Q2, Q3, Q4, Q5, Q6: BC817; SOT23
R1, R4, R6: 4K7; R0603
R2, R5, R7: 82R; R0603
R3: 330R; R0603
U$1, U$2, U$3, U$4: M3_MOUNTING_HOLE

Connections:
+12V: J2.7, LED1.1 (CA), R3.2
C: J1.5, J2.5
GND: J1.2, J1.MP1, J1.MP2, J2.2, J2.MP1, J2.MP2, Q1.2 (E), Q3.2 (E), Q5.2 (E), R2.1, R5.1, R7.1
LED_B: J2.8, R6.1
LED_G: J2.6, R4.1
LED_R: J2.4, R1.1
unnamed: Q1.1 (B), Q6.2 (E), R2.2
unnamed: Q1.3 (C), Q6.1 (B), R1.2
unnamed: LED1.4 (G), Q4.3 (C)
unnamed: Q3.1 (B), Q4.2 (E), R5.2
unnamed: Q3.3 (C), Q4.1 (B), R4.2
unnamed: LED1.3 (R), Q6.3 (C)
unnamed: Q2.2 (E), Q5.1 (B), R7.2
unnamed: Q2.1 (B), Q5.3 (C), R6.2
unnamed: LED1.2 (B), Q2.3 (C)
unnamed: J1.1, R3.1
NC: J1.3, J2.1
NO: J1.4, J2.3


Board: 2 copper layers, 40.0 x 52.1 mm, 20 parts (1 on the bottom side), 18 nets.

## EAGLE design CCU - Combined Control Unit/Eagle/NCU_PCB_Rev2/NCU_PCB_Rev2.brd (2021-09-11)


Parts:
C1, C2, C3, C4: 0.1uF; C0603
J1: 505433-0871; 5054330871
R1: BLM18PG471SN1D; R0603
R2, R3: 10K; R0603
S1: KMR621NGLFS
SWD1: SWD_TAGCONNECTNO-LEG; TC2030-IDC-NL
U1: STM32F303K8; LQFP-32

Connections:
+3V3: C1.1, C3.1, J1.1, R1.2, R2.2, SWD1.1 (VCC), U1.1 (VDD_2), U1.17 (VDD); also elsewhere on the board
ANGLE_SENSOR: U1.6 (PA0); also elsewhere on the board
D: U1.22 (PA12); also elsewhere on the board
DRIVER_EN: U1.14 (PB0); also elsewhere on the board
GND: C1.2, C2.2, C3.2, C4.2, J1.5, J1.MP1, J1.MP2, R3.2, S1.1, S1.2, SWD1.5 (GND), U1.16 (VSS_2), U1.32 (VSS); also elsewhere on the board
INPUT_1: U1.11 (PA5); also elsewhere on the board
INPUT_2: U1.10 (PA4); also elsewhere on the board
LEFT_STEP: U1.29 (PB6); also elsewhere on the board
unnamed: C2.1, R1.1, U1.5 (VDDA/VREF+)
unnamed: R3.1, U1.31 (BOOT0)
NRST: C4.1, J1.3, R2.1, S1.3, S1.4, SWD1.3 (!RST), U1.4 (NRST)
R: U1.21 (PA11); also elsewhere on the board
RIGHT_STEP: U1.30 (PB7); also elsewhere on the board
RS: U1.3 (PF1-OSC_OUT); also elsewhere on the board
RX1: U1.20 (PA10); also elsewhere on the board
RX2: J1.7, U1.25 (PA15)
STM_12_INDIC: U1.7 (PA1); also elsewhere on the board
SWDCLK: J1.4, SWD1.4 (SWDCLK), U1.24 (PA14)
SWDIO: J1.2, SWD1.2 (SWDIO), U1.23 (PA13)
SWO: J1.6, SWD1.6 (SWO), U1.26 (PB3)
TX1: U1.19 (PA9); also elsewhere on the board
TX2: J1.8, U1.8 (PA2)

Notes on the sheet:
Autonomous WaveRunner - NCU
Rev2, 2021.03.04
Benjamin Lundgren, Noel Danielsson, Viktor Lindström
Pindef Nucleo: D1 - PA9 D2 - PA12 D3 - PB0 D4 - PB7 D5 - PB6 D6 - PB1 D7 - PF0 D8 - PF1 D9 - PA8 D10 - PA11 D11 - PB5 D12 - PB4 D13 - PB3
A1 - PA1 A2 - PA3 A3 - PA4 A4 - PA5 A5 - PA6 A6 - PA7 A7 - PA2
NCU - Microcontroller, SWD, RX_TX
Programming header
SWD header
Reset button


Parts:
C5, C7, C9, C14, C16, C17, C18: 10uF; C1206
C6: 100uF; PANASONIC_C
C8: 100nF; C0603
C10: 3.3nF; C0603
C11: 10uF; C0805
C12: 22uF; C0805
C15: 1uF; C0805
C19, C20: 10nF; C0603
D1: 3.3V-POW; CHIP-LED0805
D2: 5V-POW; CHIP-LED0805
D3: 12V-POW; CHIP-LED0805
D4: 12V_AUTO-POW; CHIP-LED0805
IC1: LMZ21700SILT; SIL0008E
IC4: LTC3260EMSE#PBF; SOP50P490X110-17N
R4: 44K2 1%; R0603
R5: 10K 1%; R0603
R6: 232K 1%; R0603
R7: 3K9; R0603
R8: 1K1; R0603
R9: 15K; R0603
R10: 1K6; R0603
R11, R12: 4K3; R0603
R20, R23: 909K; R0603
R21, R22: 100K; R0603
U2: LD1117S33TR; SOT230P700X180-4N

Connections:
12V: C5.1, C7.1, C9.1, IC1.7 (EN), IC1.8 (VIN), R11.2; also elsewhere on the board
+3V3: C11.1, R8.2, U2.2 (VOUT_2), U2.4 (VOUT); also elsewhere on the board
+5V: C6.+, C8.1, C12.1, IC1.4 (VOUT), IC1.6 (VOS), R5.1, R6.1, R10.2, U2.3 (VIN); also elsewhere on the board
+12V: C14.1, IC4.11 (VIN), R9.2, R12.2; also elsewhere on the board
+24V: C17.1, IC4.12 (LDO+), R20.2; also elsewhere on the board
GND: C5.2, C6.-, C7.2, C8.2, C9.2, C10.2, C11.2, C12.2, C14.2, C16.1, C17.2, C18.1, C19.2, C20.2, D1.C (K), D2.C (K), D3.C (K), D4.C (K), IC1.5 (GND), IC1.9 (GND_(EP)_1), IC1.10 (GND_(EP)_2), IC4.2 (RT), IC4.14 (MODE), IC4.17 (GND), R4.2, R7.1, R21.1, R22.2, U2.1 (GND); also elsewhere on the board
GNDA: C18.2, IC4.5 (LDO-), R23.1; also elsewhere on the board
unnamed: D4.A, R12.1
unnamed: IC1.2 (FB), R4.1, R6.2
unnamed: C10.1, IC1.1 (SS)
unnamed: C15.2, IC4.10 (C+)
unnamed: C15.1, IC4.7 (C-)
unnamed: C20.1, IC4.16 (BYP+)
unnamed: D3.A, R11.1
unnamed: IC1.3 (PG), R5.2
unnamed: C19.1, IC4.3 (BYP-)
unnamed: C16.2, IC4.6 (VOUT)
unnamed: IC4.15 (ADJ+), R20.1, R21.2
unnamed: IC4.4 (ADJ-), R22.1, R23.2
unnamed: D2.A, R10.1
unnamed: D1.A, R8.1
STM_12_INDIC: R7.2, R9.1; also elsewhere on the board

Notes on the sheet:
Autonomous WaveRunner - NCU
Rev2, 2021.03.04
Benjamin Lundgren, Noel Danielsson, Viktor Lindström
Status LEDs
NCU - Power, Status LEDs
Voltage regulator 5V -> 3.3V
DC-DC Converter for 12V -> 5V
12V indicator, can be used to see if the motor is started, if the external system is enabled
Charge pump for mode LED 12V -> +/-12V
3mA

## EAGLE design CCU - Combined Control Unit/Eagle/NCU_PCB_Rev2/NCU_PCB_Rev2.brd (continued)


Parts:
CON1, CON2: EH_B3B-EH; B3B-EH
HOLE1, HOLE2, HOLE3, HOLE4: M3_MOUNTING_HOLE
IC2: ADM3485EARZ; SOIC127P600X175-8N
J2, J4: B4P-VH_LF__SN_; SHDR4W114P0X396_1X4_1578X850X9
J3: DT15-12PB; TE_DT15-12PB
MOD1: TMCM-1260; TMCM_1260
Q1, Q2: BSS138LT3G; SOT23
R13: 6K8; R0603
R14: 2K7; R0603
R15, R17: 680R; R0603
R16: 120R; R0603
R24, R25: 10K; R0603

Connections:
12V: J3.2; also elsewhere on the board
+3V3: IC2.8 (VCC), J3.4, J3.6, R15.1; also elsewhere on the board
+5V: J4.4; also elsewhere on the board
+12V: J4.2, J4.3; also elsewhere on the board
+24V: CON2.1; also elsewhere on the board
ANGLE_SENSOR: R13.1, R14.2; also elsewhere on the board
DRIVER_EN: IC2.2 (!RE), IC2.3 (DE); also elsewhere on the board
GND: CON1.1, IC2.5 (GND), J3.3, J3.8, J4.1, R13.2, R17.2, R24.2, R25.2; also elsewhere on the board
GNDA: Q1.2 (S), Q2.2 (S); also elsewhere on the board
INPUT_1: J3.7; also elsewhere on the board
INPUT_2: J3.5; also elsewhere on the board
LEFT_STEP: Q2.1 (G), R24.1; also elsewhere on the board
MOTOR_A1: J2.3, J3.10
MOTOR_A2: J2.4, J3.9
MOTOR_B1: J2.1, J3.12
MOTOR_B2: J2.2, J3.11
unnamed: CON1.3, IC2.7 (B), R15.2, R16.1
unnamed: J3.1, R14.1
unnamed: CON1.2, IC2.6 (A), R16.2, R17.1
unnamed: CON2.2, Q1.3 (D)
unnamed: CON2.3, Q2.3 (D)
RIGHT_STEP: Q1.1 (G), R25.1; also elsewhere on the board
RX1: IC2.1 (RO); also elsewhere on the board
TX1: IC2.4 (DI); also elsewhere on the board

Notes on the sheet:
Autonomous WaveRunner - NCU
Rev2, 2021.03.04
Benjamin Lundgren, Noel Danielsson, Viktor Lindström
NCU - Stepper motor driver
Skall till DEUTSCH
Power connector
Motor connector
RS485 connector
Direct step control (IO Header)


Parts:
C13: 0.1uF; C0603
D5: SZNUP2105LT1G; SOT96P237X111-3N
H1, H2, H3, H4, H5: S8131-46R; S813146R
HOLE5, HOLE6, HOLE7, HOLE8, HOLE9, HOLE10, HOLE11, HOLE12, HOLE13, HOLE14, HOLE15, HOLE16: M3_MOUNTING_HOLE
IC3: SN65HVD230DR; SOT127P600X175-8N
J5: M300-MV31045M1; M300MV31045M1
R18: -; R0603
R19: 0R; R0603

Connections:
12V: J5.3, J5.8; also elsewhere on the board
+3V3: C13.2, IC3.3 (VCC); also elsewhere on the board
+12V: J5.5, J5.10; also elsewhere on the board
CAN_N: D5.2 (K_2), IC3.6 (CANL), J5.6
CAN_P: D5.1 (K_1), IC3.7 (CANH), J5.1
D: IC3.1 (D); also elsewhere on the board
GND: C13.1, D5.3 (K_3), IC3.2 (GND), J5.2, J5.4, J5.7, J5.9, R19.1; also elsewhere on the board
unnamed: IC3.8 (RS), R18.1, R19.2
R: IC3.4 (R); also elsewhere on the board
RS: R18.2; also elsewhere on the board

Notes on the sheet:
Benjamin Lundgren, Noel Danielsson, Viktor Lindström
NCU - CAN bus/DB, Mounting holes, Cable mounts
DB: 1. CAN_H 6. CAN_L 2-7. GND 3-8. 12V 4-9. GND 5-10. 12V_AUTO
Autonomous WaveRunner - NCU
Rev2, 2021.03.04


Board: 4 copper layers, 110.9 x 78.2 mm, 89 parts (1 on the bottom side), 53 nets.

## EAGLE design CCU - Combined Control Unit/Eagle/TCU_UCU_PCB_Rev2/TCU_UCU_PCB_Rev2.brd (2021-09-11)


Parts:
C1, C2, C3, C4: 0.1uF; C0603
J1: 505433-0871; 5054330871
R1: BLM18PG471SN1D; R0603
R2, R3: 10K; R0603
S3: KMR621NGLFS
SWD1: SWD_TAGCONNECTNO-LEG; TC2030-IDC-NL
U1: STM32F303K8; LQFP-32
U2: TL074ID; SOIC127P600X175-14N

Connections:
+3V3: C1.1, C3.1, J1.1, R1.2, R2.2, SWD1.1 (VCC), U1.1 (VDD_2), U1.17 (VDD); also elsewhere on the board
+9V: U2.4 (VCC+); also elsewhere on the board
-9V: U2.11 (VCC-); also elsewhere on the board
APSFC_STM_ANOUT: U2.6 (2IN-), U2.7 (2OUT); also elsewhere on the board
APSFC_STM_IN: U1.7 (PA1); also elsewhere on the board
APS_STM_ANOUT: U2.1 (1OUT), U2.2 (1IN-); also elsewhere on the board
APS_STM_IN: U1.9 (PA3); also elsewhere on the board
D_TCU: U1.22 (PA12); also elsewhere on the board
GND: C1.2, C2.2, C3.2, C4.2, J1.5, J1.MP1, J1.MP2, R3.2, S3.1, S3.2, SWD1.5 (GND), U1.16 (VSS_2), U1.32 (VSS); also elsewhere on the board
unnamed: U1.11 (PA5), U2.5 (2IN+)
unnamed: U1.12 (PA6), U2.3 (1IN+)
unnamed: U1.10 (PA4), U2.10 (3IN+)
unnamed: C2.1, R1.1, U1.5 (VDDA/VREF+)
unnamed: R3.1, U1.31 (BOOT0)
NRST_TCU: C4.1, J1.3, R2.1, S3.3, S3.4, SWD1.3 (!RST), U1.4 (NRST)
RPS_STM_ANOUT: U2.8 (3OUT), U2.9 (3IN-); also elsewhere on the board
RPS_STM_IN: U1.6 (PA0); also elsewhere on the board
RS_TCU: U1.3 (PF1-OSC_OUT); also elsewhere on the board
RX_TCU: J1.7, U1.25 (PA15)
R_TCU: U1.21 (PA11); also elsewhere on the board
STM_12_INDIC: U1.14 (PB0); also elsewhere on the board
SWDCLK_TCU: J1.4, SWD1.4 (SWDCLK), U1.24 (PA14)
SWDIO_TCU: J1.2, SWD1.2 (SWDIO), U1.23 (PA13)
SWO_TCU: J1.6, SWD1.6 (SWO), U1.26 (PB3)
TX_TCU: J1.8, U1.8 (PA2)

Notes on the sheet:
Autonomous WaveRunner - TCU
Rev 3, 2020-02-01
Benjamin Lundgren, Noel Danielsson, Viktor Lindström
Buffer for DAC1_OUT1/2, DAC2_OUT1
Pindef Nucleo: D1 - PA9 D2 - PA12 D3 - PB0 D4 - PB7 D5 - PB6 D6 - PB1 D7 - PF0 D8 - PF1 D9 - PA8 D10 - PA11 D11 - PB5 D12 - PB4 D13 - PB3
A1 - PA1 A2 - PA3 A3 - PA4 A4 - PA5 A5 - PA6 A6 - PA7 A7 - PA2
TCU - Microcontroller, SWD, RX_TX
Programming header
SWD header
Reset button


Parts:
AC1: ADXL377BCPZ-RL7; QFN50P300X300X150-17N
C33, C34, C35, C36, C40: 0.1uF; C0603
C37, C38, C39: 50nF; C0603
J3: 505433-0871; 5054330871
R64: BLM18PG471SN1D; R0603
R68, R69: 10K; R0603
S1: KMR621NGLFS
SWD2: SWD_TAGCONNECTNO-LEG; TC2030-IDC-NL
U6: STM32F303K8; LQFP-32

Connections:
+3V3: AC1.14 (VS_1), AC1.15 (VS_2), C33.1, C34.1, C40.2, J3.1, R64.2, R69.2, SWD2.1 (VCC), U6.1 (VDD_2), U6.17 (VDD); also elsewhere on the board
ACC_ST: AC1.2 (ST), U6.27 (PB4)
ACC_X: AC1.5 (XOUT), C39.2, U6.6 (PA0)
ACC_Y: AC1.4 (YOUT), C38.2, U6.7 (PA1)
ACC_Z: AC1.16 (ZOUT), C37.2, U6.9 (PA3)
BUZZER_EN: U6.10 (PA4); also elsewhere on the board
BUZZER_ON: U6.18 (PA8); also elsewhere on the board
D_UCU: U6.22 (PA12); also elsewhere on the board
GND: AC1.6 (GND_1), AC1.7 (GND_2), AC1.17 (THERMAL_PAD), C33.2, C34.2, C35.2, C36.2, C37.1, C38.1, C39.1, C40.1, J3.5, J3.MP1, J3.MP2, R68.2, S1.1, S1.2, SWD2.5 (GND), U6.16 (VSS_2), U6.32 (VSS); also elsewhere on the board
unnamed: C35.1, R64.1, U6.5 (VDDA/VREF+)
unnamed: R68.1, U6.31 (BOOT0)
NRST_UCU: C36.1, J3.3, R69.1, S1.3, S1.4, SWD2.3 (!RST), U6.4 (NRST)
RS_UCU: U6.3 (PF1-OSC_OUT); also elsewhere on the board
RX_UCU: J3.7, U6.25 (PA15)
R_UCU: U6.21 (PA11); also elsewhere on the board
SPEED_SENS_IN: U6.15 (PB1); also elsewhere on the board
STM_12_INDIC: U6.14 (PB0); also elsewhere on the board
SWDCLK_UCU: J3.4, SWD2.4 (SWDCLK), U6.24 (PA14)
SWDIO_UCU: J3.2, SWD2.2 (SWDIO), U6.23 (PA13)
SWO_UCU: J3.6, SWD2.6 (SWO), U6.26 (PB3)
TX_UCU: J3.8, U6.8 (PA2)

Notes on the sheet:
Autonomous WaveRunner - TCU
Rev 3, 2020-02-01
Benjamin Lundgren, Noel Danielsson, Viktor Lindström
UCU - Microcontroller, SWD, RX_TX
Programming header
SWD header
Reset button
Pindef Nucleo: D1 - PA9 D2 - PA12 D3 - PB0 D4 - PB7 D5 - PB6 D6 - PB1 D7 - PF0 D8 - PF1 D9 - PA8 D10 - PA11 D11 - PB5 D12 - PB4 D13 - PB3
A1 - PA1 A2 - PA3 A3 - PA4 A4 - PA5 A5 - PA6 A6 - PA7 A7 - PA2


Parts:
C5: 100uF; PANASONIC_C
C6: 100nF; C0603
C7: 10uF; C0805
C18: 3.3nF; C0603
C19: 22uF; C0805
C21, C22, C23, C24, C26, C27, C28: 10uF; C1206
C25: 1uF; C0805
C29, C30: 10nF; C0603
D1: 12V_AUTO-POW; CHIP-LED0805
D2: 12V-POW; CHIP-LED0805
D3: 5V-POW; CHIP-LED0805
D4: 3.3V-POW; CHIP-LED0805
IC3: LTC3260EMSE#PBF; SOP50P490X110-17N
IC4: LMZ21700SILT; SIL0008E
R4, R55: 1.3M; R0603
R6, R7: 4K3; R0603
R8: 1K6; R0603
R9: 1K1; R0603
R10: 10K 1%; R0603
R11: 232K 1%; R0603
R12: 44K2 1%; R0603
R53, R54: 200K; R0603
R70: 15K; R0603
R71: 3K9; R0603
U3: LD1117S33TR; SOT230P700X180-4N

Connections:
12V: C21.1, C22.1, C23.1, C24.1, IC3.1 (EN+), IC3.11 (VIN), IC3.13 (EN-), IC4.7 (EN), IC4.8 (VIN), R7.2; also elsewhere on the board
+3V3: C7.1, R9.2, U3.2 (VOUT_2), U3.4 (VOUT); also elsewhere on the board
+5V: C5.+, C6.1, C19.1, IC4.4 (VOUT), IC4.6 (VOS), R8.2, R10.1, R11.1, U3.3 (VIN); also elsewhere on the board
+9V: C27.1, IC3.12 (LDO+), R4.2; also elsewhere on the board
+12V: R6.2, R70.2; also elsewhere on the board
-9V: C28.2, IC3.5 (LDO-), R55.1; also elsewhere on the board
GND: C5.-, C6.2, C7.2, C18.2, C19.2, C21.2, C22.2, C23.2, C24.2, C26.1, C27.2, C28.1, C29.2, C30.2, D1.C (K), D2.C (K), D3.C (K), D4.C (K), IC3.2 (RT), IC3.14 (MODE), IC3.17 (GND), IC4.5 (GND), IC4.9 (GND_(EP)_1), IC4.10 (GND_(EP)_2), R12.2, R53.1, R54.2, R71.1, U3.1 (GND); also elsewhere on the board
unnamed: C25.2, IC3.10 (C+)
unnamed: D1.A, R6.1
unnamed: IC4.2 (FB), R11.2, R12.1
unnamed: C18.1, IC4.1 (SS)
unnamed: D2.A, R7.1
unnamed: IC4.3 (PG), R10.2
unnamed: C25.1, IC3.7 (C-)
unnamed: C26.2, IC3.6 (VOUT)
unnamed: IC3.15 (ADJ+), R4.1, R53.2
unnamed: IC3.4 (ADJ-), R54.1, R55.2
unnamed: D3.A, R8.1
unnamed: C30.1, IC3.16 (BYP+)
unnamed: C29.1, IC3.3 (BYP-)
unnamed: D4.A, R9.1
STM_12_INDIC: R70.1, R71.2; also elsewhere on the board

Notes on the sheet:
Charge pump for OP-Amps 12V -> +/-9V
Status LEDs
Autonomous WaveRunner - TCU
Rev 3, 2020-02-01
Benjamin Lundgren, Noel Danielsson, Viktor Lindström
TCU/UCU - Power, Status LEDs
Voltage regulator 5V -> 3.3V
DC-DC Converter for 12V -> 5V
12V indicator, can be used to see if the motor is started, if the external system is enabled


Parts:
C8, C9, C10, C11: 0.1uF; C0805
R14, R15, R16, R22, R23, R24, R34, R35, R42, R43: 4k7; R0603
R17, R18, R19, R20, R25, R26, R27, R28, R30, R31, R36, R37, R38, R39, R44, R45: 6k8; R0603
R21, R29, R32, R33, R40, R41: 3k9; R0603
U4, U5: TL074ID; SOIC127P600X175-14N

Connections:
+9V: C8.1, C9.1, U4.4 (VCC+), U5.4 (VCC+); also elsewhere on the board
-9V: C10.1, C11.1, U4.11 (VCC-), U5.11 (VCC-); also elsewhere on the board
APS1_GND: R17.2, R26.1; also elsewhere on the board
APS1_IN: R25.2; also elsewhere on the board
APS1_SIG_OUT: R18.1, U4.1 (1OUT); also elsewhere on the board
APS2_GND: R27.1; also elsewhere on the board
APS2_SIG_OUT: R19.1, U4.7 (2OUT); also elsewhere on the board
APSFC_GND: R28.1, R44.2; also elsewhere on the board
APSFC_IN: R36.2; also elsewhere on the board
APSFC_SIG_OUT: R20.1, U5.1 (1OUT); also elsewhere on the board
APSFC_STM_ANOUT: R24.2; also elsewhere on the board
APSFC_STM_IN: R40.1, U5.14 (4OUT); also elsewhere on the board
APS_STM_ANOUT: R22.2, R23.2; also elsewhere on the board
APS_STM_IN: R21.1, U5.7 (2OUT); also elsewhere on the board
GND: C8.2, C9.2, C10.2, C11.2, R14.2, R15.2, R16.2, R29.1, R32.1, R33.1, R42.2, R43.2; also elsewhere on the board
unnamed: R22.1, R26.2, U4.3 (1IN+)
unnamed: R14.1, R18.2, U4.2 (1IN-)
unnamed: R31.2, R35.1, U4.10 (3IN+)
unnamed: R39.2, R43.1, U4.9 (3IN-)
unnamed: R30.2, R34.1, U4.12 (4IN+)
unnamed: R38.2, R42.1, U4.13 (4IN-)
unnamed: R23.1, R27.2, U4.5 (2IN+)
unnamed: R15.1, R19.2, U4.6 (2IN-)
unnamed: R24.1, R28.2, U5.3 (1IN+)
unnamed: R16.1, R20.2, U5.2 (1IN-)
unnamed: R33.2, R37.1, U5.10 (3IN+)
unnamed: R41.2, R45.1, U5.9 (3IN-)
unnamed: R32.2, R36.1, U5.12 (4IN+)
unnamed: R40.2, R44.1, U5.13 (4IN-)
unnamed: R25.1, R29.2, U5.5 (2IN+)
unnamed: R17.1, R21.2, U5.6 (2IN-)
RPS1_GND: R30.1, R45.2; also elsewhere on the board
RPS1_IN: R37.2; also elsewhere on the board
RPS1_SIG_OUT: R38.1, U4.14 (4OUT); also elsewhere on the board
RPS2_GND: R31.1; also elsewhere on the board
RPS2_SIG_OUT: R39.1, U4.8 (3OUT); also elsewhere on the board
RPS_STM_ANOUT: R34.2, R35.2; also elsewhere on the board
RPS_STM_IN: R41.1, U5.8 (3OUT); also elsewhere on the board

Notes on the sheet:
Input circuit to STM
Output circuit from STM
Difference amplifier circuits consisting of two quad OP-amps with +/- 9V input. Compensates for different potentials in the Exsisting and Added system. Also shifts the signal level from and to the STM between 3.3V and 5V Consists of: 5x Output circuits from STM 3x Input circuits to STM
Autonomous WaveRunner - TCU
Rev 3, 2020-02-01
Benjamin Lundgren, Noel Danielsson, Viktor Lindström
TCU - Difference amplifier circuits


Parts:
C31: 10 uF; C0805
C32: -; C1206
D10: PMEG4010; SOD123
K4: V23079A1001B301; 413937885
Q2, Q4, Q5, Q6: 2N7002PW,115; SOT323
Q3, Q7: VO618A-3; DIL04-400
R56, R62, R63, R65: 10K; R0603
R61, R67: 100K; R0603
R66: 113K; R0603

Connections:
12V: K4.8 (NO_2); also elsewhere on the board
+3V3: R65.2; also elsewhere on the board
+5V: D10.C, K4.1 (+), R61.1; also elsewhere on the board
BUZZER_EN: Q5.1 (G), R62.1; also elsewhere on the board
BUZZER_ON: Q6.1 (G), R63.1; also elsewhere on the board
BUZ_ECM_12V: K4.10 (NC_2), Q3.1 (1A); also elsewhere on the board
BUZ_ECM_GND: K4.3 (NC_1), R56.1; also elsewhere on the board
BUZ_STE_12V: K4.9 (COM_2); also elsewhere on the board
BUZ_STE_GND: K4.4 (COM_1); also elsewhere on the board
GND: C31.2, C32.2, Q3.3 (3E), Q5.2 (S), Q6.2 (S), Q7.3 (3E), R62.2, R63.2; also elsewhere on the board
unnamed: Q2.3 (D), Q7.2 (2C)
unnamed: Q7.1 (1A), R66.2
unnamed: C31.1, C32.1, Q3.4 (4C), Q4.1 (G), R61.2
unnamed: D10.A, K4.12 (-), Q4.3 (D)
unnamed: Q4.2 (S), Q5.3 (D)
unnamed: K4.5 (NO_1), Q6.3 (D)
unnamed: Q3.2 (2C), R56.2
SPEED_SENS_12V: R66.1; also elsewhere on the board
SPEED_SENS_GND: Q2.2 (S), R67.1; also elsewhere on the board
SPEED_SENS_IN: Q7.4 (4C), R65.1; also elsewhere on the board
SPEED_SENS_SIG: Q2.1 (G), R67.2; also elsewhere on the board

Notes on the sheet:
Buzzer, original system always overrides the external system
Autonomous WaveRunner - TCU
Rev 3, 2020-02-01
Benjamin Lundgren, Noel Danielsson, Viktor Lindström
Optocoupler for reading the SPEED SENSOR signal
UCU - Buzzer logic, Speed sensor


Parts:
C12, C13, C14, C15, C16: 10 uF; C0805
D5, D6, D7: PMEG4010; SOD123
FRONT_CONNECTOR: DRC22-50P01; TE_DRC22-50P01
K1, K2, K3: V23079A1003B301; 413937885
R46, R47, R48, R49, R50: 200R; R0603

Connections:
+3V3: K3.8 (NO_2); also elsewhere on the board
+12V: D5.C, D6.C, D7.C, K1.1 (+), K2.1 (+), K3.1 (+); also elsewhere on the board
APS1_GND: C14.1, FRONT_CONNECTOR.24, FRONT_CONNECTOR.33; also elsewhere on the board
APS1_IN: FRONT_CONNECTOR.42, K2.3 (NC_1); also elsewhere on the board
APS1_OUT: C14.2, FRONT_CONNECTOR.14, R48.1
APS1_SIG_OUT: K2.5 (NO_1); also elsewhere on the board
APS1_VCC: FRONT_CONNECTOR.34, FRONT_CONNECTOR.43
APS2_GND: C15.1, FRONT_CONNECTOR.13, FRONT_CONNECTOR.22; also elsewhere on the board
APS2_IN: FRONT_CONNECTOR.41, K2.10 (NC_2)
APS2_OUT: C15.2, FRONT_CONNECTOR.4, R49.1
APS2_SIG_OUT: K2.8 (NO_2); also elsewhere on the board
APS2_VCC: FRONT_CONNECTOR.23, FRONT_CONNECTOR.32
APSFC_GND: C16.1, FRONT_CONNECTOR.2, FRONT_CONNECTOR.11; also elsewhere on the board
APSFC_IN: FRONT_CONNECTOR.31, K3.3 (NC_1); also elsewhere on the board
APSFC_OUT: C16.2, FRONT_CONNECTOR.3, R50.1
APSFC_SIG_OUT: K3.5 (NO_1); also elsewhere on the board
APSFC_VCC: FRONT_CONNECTOR.12, FRONT_CONNECTOR.21
BUZ_ECM_12V: FRONT_CONNECTOR.16; also elsewhere on the board
BUZ_ECM_GND: FRONT_CONNECTOR.17; also elsewhere on the board
BUZ_STE_12V: FRONT_CONNECTOR.6; also elsewhere on the board
BUZ_STE_GND: FRONT_CONNECTOR.7; also elsewhere on the board
GND: D5.A, D6.A, D7.A, K1.12 (-), K2.12 (-), K3.12 (-); also elsewhere on the board
unnamed: K1.4 (COM_1), R46.2
unnamed: K1.9 (COM_2), R47.1
unnamed: K2.4 (COM_1), R48.2
unnamed: K2.9 (COM_2), R49.2
unnamed: K3.4 (COM_1), R50.2
RPS1_GND: C12.1, FRONT_CONNECTOR.38, FRONT_CONNECTOR.49; also elsewhere on the board
RPS1_IN: FRONT_CONNECTOR.37, K1.3 (NC_1); also elsewhere on the board
RPS1_OUT: C12.2, FRONT_CONNECTOR.50, R46.1
RPS1_SIG_OUT: K1.5 (NO_1); also elsewhere on the board
RPS1_VCC: FRONT_CONNECTOR.47, FRONT_CONNECTOR.48
RPS2_GND: C13.1, FRONT_CONNECTOR.29, FRONT_CONNECTOR.30; also elsewhere on the board
RPS2_IN: FRONT_CONNECTOR.27, K1.10 (NC_2)
RPS2_OUT: C13.2, FRONT_CONNECTOR.40, R47.2
RPS2_SIG_OUT: K1.8 (NO_2); also elsewhere on the board
RPS2_VCC: FRONT_CONNECTOR.28, FRONT_CONNECTOR.39
SPEED_SENS_12V: FRONT_CONNECTOR.8, FRONT_CONNECTOR.18; also elsewhere on the board
SPEED_SENS_GND: FRONT_CONNECTOR.9, FRONT_CONNECTOR.19; also elsewhere on the board
SPEED_SENS_SIG: FRONT_CONNECTOR.10, FRONT_CONNECTOR.20; also elsewhere on the board
STM_12_INDIC: K3.9 (COM_2); also elsewhere on the board

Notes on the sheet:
Lowpass filters
Relays for switching between MAN and EXT mode
Autonomous WaveRunner - TCU
Rev 3, 2020-02-01
Benjamin Lundgren, Noel Danielsson, Viktor Lindström
Connectors for APS and RPS from the HANDLE and ECM. Relays to switch mode between MANUAL and EXTERNAL depending on the 12V input. Lowpass filters to make the transition smoother.
RPS_HANDLE (IN): - RPS1: 1-3 - RPS2: 4-6 RPS_ECM (OUT): - RPS1: 7-9 - RPS2: 10-12
APS_HANDLE (IN): - APS1: 1-3 - APS2: 4-6 - APSFC: 7-9 APS_ECM (OUT): - APS1: 10-12 - APS2: 1-3 - APSFC: 4-6
TCU/UCU - APS/RPS Logic with Safety relays, Front connector


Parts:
C17, C20: 0.1uF; C0603
D8, D9: SZNUP2105LT1G; SOT96P237X111-3N
H1: S8131-46R; S813146R
IC1, IC2: SN65HVD230DR; SOT127P600X175-8N
J2: M300-MV31045M1; M300MV31045M1
R5, R51: -; R0603
R13, R52: 0R; R0603
U$1, U$2, U$3, U$4, U$5, U$6, U$7, U$8, U$9, U$10: M3_MOUNTING_HOLE

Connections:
12V: J2.3, J2.8; also elsewhere on the board
+3V3: C17.2, C20.2, IC1.3 (VCC), IC2.3 (VCC); also elsewhere on the board
+12V: J2.5, J2.10; also elsewhere on the board
CAN_N: D8.2 (K_2), D9.2 (K_2), IC1.6 (CANL), IC2.6 (CANL), J2.6
CAN_P: D8.1 (K_1), D9.1 (K_1), IC1.7 (CANH), IC2.7 (CANH), J2.1
D_TCU: IC1.1 (D); also elsewhere on the board
D_UCU: IC2.1 (D); also elsewhere on the board
GND: C17.1, C20.1, D8.3 (K_3), D9.3 (K_3), IC1.2 (GND), IC2.2 (GND), J2.2, J2.4, J2.7, J2.9, R13.1, R52.1; also elsewhere on the board
unnamed: IC1.8 (RS), R51.1, R52.2
unnamed: IC2.8 (RS), R5.1, R13.2
RS_TCU: R51.2; also elsewhere on the board
RS_UCU: R5.2; also elsewhere on the board
R_TCU: IC1.4 (R); also elsewhere on the board
R_UCU: IC2.4 (R); also elsewhere on the board

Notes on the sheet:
Autonomous WaveRunner - TCU
Rev 3, 2020-02-01
Benjamin Lundgren, Noel Danielsson, Viktor Lindström
TCU - CAN bus/iDB2
iDB2 (internal bridge): 1. CAN_H 6. CAN_L 2-7. GND 3-8. 12V 4-9. GND 5-10. 12V_AUTO
Strong pull down to GND => CAN high speed mode


Board: 4 copper layers, 110.9 x 78.2 mm, 157 parts (1 on the bottom side), 124 nets.

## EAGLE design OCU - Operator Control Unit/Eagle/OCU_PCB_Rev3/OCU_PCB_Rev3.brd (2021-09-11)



Board: 2 copper layers, 112.0 x 116.0 mm, 122 parts (4 on the bottom side), 79 nets.

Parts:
C1, C2, C3, C4, C21: 0.1uF; C0603
C5, C6, C8, C9, C10, C14, C15: 10uF; C1206
C7: 1uF; C0805
C11: 3.3nF; C0603
C12, C13: 10nF; C0603
C16: 22uF; C0805
C17: 100uF; PANASONIC_C
C18: 100nF; C0603
C19: 10uF; C0805
C20: 220uF; PANASONIC_E
C22: 4.7nF; C0805
D1: 12V-POW; CHIP-LED0805
D2, D3: SOD-123
D4: SZNUP2105LT1G; SOT96P237X111-3N
HOLE1, HOLE2, HOLE3, HOLE4, HOLE5, HOLE6, HOLE7, HOLE8, HOLE9, HOLE10, HOLE11, HOLE12, HOLE13, HOLE14, HOLE15, HOLE16: M3_MOUNTING_HOLE
IC1: LTC3260EMSE#PBF; SOP50P490X110-17N
IC2: LMZ21700SILT; SIL0008E
IC3: SN65HVD230DR; SOT127P600X175-8N
J1: DT15-2P; DT152P
J2: DT15-4P; DT154P
J3: 43045-0413; 430450413
J4: 505567-0371; 5055680371
J5: 43045-0213
J6, J8: 505567-0271; 5055680271
J7: 505433-0871; 5054330871
J9, J10: DT15-6P; TE_DT15-6P
K1: V23079A1003B301; 413937885
Q1: VO618A-3; DIL04-400
R1: BLM18PG471SN1D; R0603
R2, R3, R17, R18: 10K; R0603
R4, R7: 909K; R0603
R5, R6: 100K; R0603
R8: 44K2 1%; R0603
R9: 10K 1%; R0603
R10: 232K 1%; R0603
R11: 3K9; R0603
R12: 15K; R0603
R13: 820R; R0603
R14: 4K7; R0603
R15: 9K1; R0603
R16: 1K5; R0603
R19: -; R0603
R20, R25: 0R; R0603
R21, R22, R23, R24: 120R; R1210
S1: KMR621NGLFS
ST_LINK1:C2, ST_LINK1:C19, ST_LINK1:C22, ST_LINK1:C23, ST_LINK1:C24: 0.1uF; C0603
ST_LINK1:C3: 10uF; C0603
ST_LINK1:C20, ST_LINK1:C21: 10pF; C0603
ST_LINK1:D1, ST_LINK1:D2, ST_LINK1:D3: CHIP-LED0805
ST_LINK1:F1: OZCJ0050; OZCJ
ST_LINK1:FP1: R0603
ST_LINK1:IC3: STM32F103CBT6TR; QFP50P900X900X160-48N
ST_LINK1:J1: 505568-0571; 5055680571
ST_LINK1:Q1: 2N7002PW,115; SOT323
ST_LINK1:Q2: BC817; SOT23
ST_LINK1:R1: 0; R0603
ST_LINK1:R2, ST_LINK1:R3: 330; R0603
ST_LINK1:R4: 680; R0603
ST_LINK1:R25: 1K5; R0603
ST_LINK1:R26, ST_LINK1:R32: 10K; R0603
ST_LINK1:R27: 36K; R0603
ST_LINK1:R28: 100; R0603
ST_LINK1:R29, ST_LINK1:R33: 100K; R0603
ST_LINK1:R30, ST_LINK1:R34, ST_LINK1:R35: 4K7; R0603
ST_LINK1:R31: 2K7; R0603
ST_LINK1:R36: 100; R0805
ST_LINK1:SWD1: SWD_TAGCONNECTNO-LEG; TC2030-IDC-NL
ST_LINK1:U1: LD1117S33TR; SOT230P700X180-4N
ST_LINK1:Y2: NX3225GD-8MHZ-STD-CRA-3; RESC3226X100N
SWD1: SWD_TAGCONNECTNO-LEG; TC2030-IDC-NL
U1: STM32F303K8; LQFP-32
U2: LD1117S33TR; SOT230P700X180-4N
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

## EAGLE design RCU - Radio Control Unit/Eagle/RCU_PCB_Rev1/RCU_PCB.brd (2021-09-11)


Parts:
C1, C2, C3, C4: 0.1uF; C0603
D1: 3.3V-POW; CHIP-LED0805
D2: 5V-POW; CHIP-LED0805
D3: 12V-POW; CHIP-LED0805
IC1: SN74LVC1GU04DBVT; SOT95P280X145-5N
J3: 505567-0471; 5055680471
MOD1: FRSKY_RX8R
R1: BLM18PG471SN1D; R0603
R2, R3: 10K; R0603
R4: 220R; R0603
R5: 330R; R0603
R6: 820R; R0603
S1: KMR621NGLFS
SWD1: SWD_TAGCONNECTNO-LEG; TC2030-IDC-NL
U1: STM32F303K8; LQFP-32

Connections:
12V: R6.2; also elsewhere on the board
+3V3: C1.1, C4.1, J3.2, R1.2, R2.2, R4.2, SWD1.1 (VCC), U1.1 (VDD_2), U1.17 (VDD); also elsewhere on the board
+5V: IC1.5 (VCC), MOD1.2, R5.2; also elsewhere on the board
D: U1.22 (PA12); also elsewhere on the board
GND: C1.2, C2.2, C3.2, C4.2, D1.C (K), D2.C (K), D3.C (K), IC1.3 (GND), J3.1, J3.MP1, J3.MP2, MOD1.1, R3.2, S1.1, S1.2, SWD1.5 (GND), U1.16 (VSS_2), U1.32 (VSS); also elsewhere on the board
unnamed: D3.A, R6.1
unnamed: D2.A, R5.1
unnamed: C3.1, R1.1, U1.5 (VDDA/VREF+)
unnamed: D1.A, R4.1
unnamed: R3.1, U1.31 (BOOT0)
NRST: C2.1, R2.1, S1.3, S1.4, SWD1.3 (!RST), U1.4 (NRST)
R: U1.21 (PA11); also elsewhere on the board
RS: U1.3 (PF1-OSC_OUT); also elsewhere on the board
RX: J3.3, U1.25 (PA15)
SBUS: IC1.2 (A), MOD1.3
SBUS_INV: IC1.4 (Y), U1.20 (PA10)
SWDCLK: SWD1.4 (SWDCLK), U1.24 (PA14)
SWDIO: SWD1.2 (SWDIO), U1.23 (PA13)
SWO: SWD1.6 (SWO), U1.26 (PB3)
TX: J3.4, U1.8 (PA2)
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

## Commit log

2021-11-03 added OCU top buttons to exsisting hardware adapter
    [OCU_Buttons_Adapter_Rev1.sch]
2021-11-03 finished button adapter, started with power pcb
    [MCU_Power_PCB_Rev1.brd, MCU_Power_PCB_Rev1.sch, OCU_Buttons_Adapter_Rev1.brd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]
2021-11-05 finished board
    [MCU_Power_PCB_Rev1.brd, MCU_Power_PCB_Rev1.sch, OCU_Buttons_Adapter_Rev1.brd]
2021-12-09 updated MCU power pcb
    [MCU_Power_PCB_Rev1.brd, MCU_Power_PCB_Rev1.sch]
2022-08-03 Added LED driver PCBA
    [LED-Driver.kicad_pcb, LED-Driver.sch, TPS25940x-Q1.sch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]

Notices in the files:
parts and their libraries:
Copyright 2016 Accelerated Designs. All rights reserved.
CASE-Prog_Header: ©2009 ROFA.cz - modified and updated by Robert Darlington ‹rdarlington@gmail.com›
